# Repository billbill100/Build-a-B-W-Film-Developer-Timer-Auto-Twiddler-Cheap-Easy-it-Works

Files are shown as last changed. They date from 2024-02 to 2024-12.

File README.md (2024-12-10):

# Build-a-B-W-Film-Developer-Timer-Auto-Twiddler-Cheap-Easy-it-Works

Following on from my successful 'Build a shutter tester for focal plane shutters, cheap, easy & it works'

Here is my design of a timer for B&W film developing.

Many, like myself, use a stopwatch or a three line LCD timer, however, I thought it would be good to move into the 21st century with a colour screen & better functionality.

The developing timer allows the user to easily program the, initial & secondary agitations and interval, as well as stop & fix times, by turning a dial.

The screen then steps though each process, showing green when running, yellow to give a 10 second warning of an action to take place (agitation for example)
and then highlighted as the user has to carry out the action. Finished tasks then become grey. An audible cue will also be added.

Additionally, for twiddlers like myself, the timer drives a stepper motor to carry out all of the development agitation tasks & also stop & fix agitation if required. I will leave the debate as to whether to twiddle or not, to others.
Myself, I find it much easier to leave the developing tank in the water bath and twiddle. It maintains a better temperature, does not aerate the developer, stops water dripping & alleviates the threat of spillage during agitations.

The hardware is all cheaply available on Aliexpress & uses many of the same parts as the shutter tester. Where possible, I have kept the wiring identical.
Basic practical skills are required to build the timer. All of the required electronic modules are pre-built, so there is little or no soldering required, as push-fit or screw terminals are used for the connections.

Optionally, a li-po battery can be added, which is automatically charged & will power the timer in the event of a power failure.

Forum can be found here
https://www.photrio.com/forum/threads/build-a-b-w-film-developing-timer-twiddler-cheap-easy-it-works.204682/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

On first startup, the screen will show an Authorisation Code and ask that a User Key be entered. To obtain the User Key, contact me via message and the key will be issued free of charge. Please note this key is will last the lifetime of your project. It only needs entering once but make a note of it (write on a piece of paper & leave in the project box) in case a Factory Reset is performed.

The User key is issued free of charge, and there will never be any charge made for this key. It has been added to stop piracy and users being charged for firmware downloads.

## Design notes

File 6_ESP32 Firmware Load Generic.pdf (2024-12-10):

### ESP32 Firmware Load. Generic V1.0 27/10/2024

Download the code from the required github page.

click on the green <>Code button, which will allow you to download all of the files as a zip file. Unzip (extract) the downloaded file.
https://github.com/billbill100
Download the Flashing software.

A program called Flash Download Tool is required. It is included on the Github page, or can be downloaded from
Tools | Espressif Systems (https://www.espressif.com/en/support/download/other-tools)

Unzip (extract) the folder and put the files somewhere suitable on the computer. The software is stand-alone and does not need to be installed.
Checking the ESP32 USB driver.

The USB driver should have been installed, following the driver installation guide. To confirm, after connecting the ESP32 board, press Windows key + x and select Device Manager. Look for the COM ports and expand. The ESP module should be seen, as in this example on COM port 6, showing the CP2102 driver.

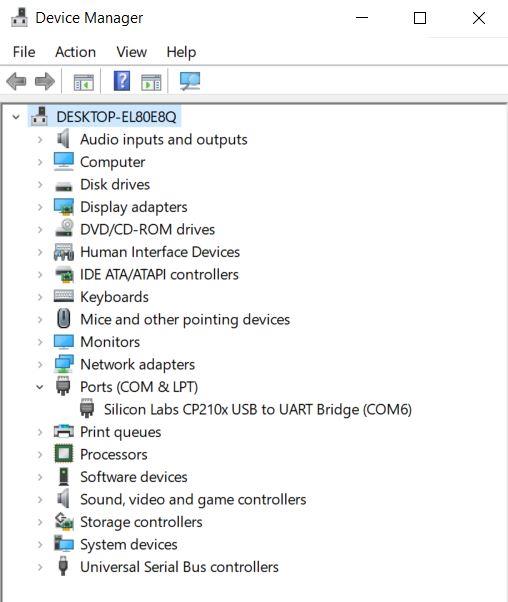
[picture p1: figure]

If the driver is missing, as shown on the screen below (Yellow Triangle) refer to the document Installing CP2102 Driver. Found in the Github repository.

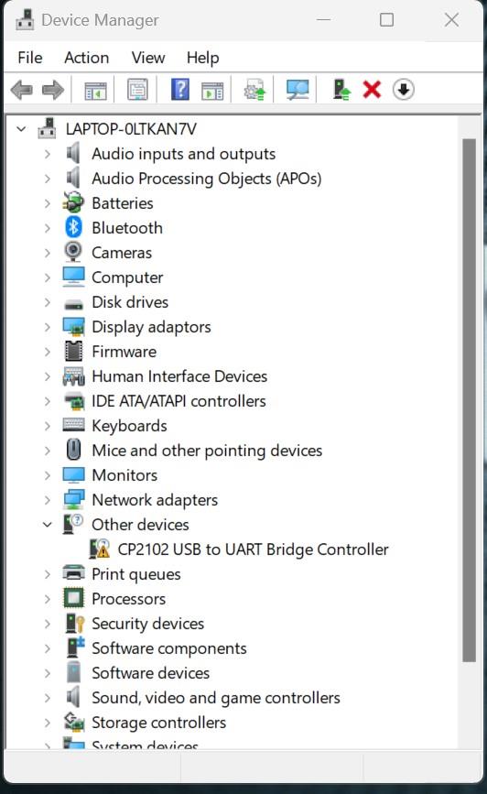
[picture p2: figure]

### Flash the Shutter Tester firmware to ESP32

Find the folder where the Flash Download Tool files were extracted to.

Launch the Flash Download Tool by double clicking on ‘flash_download_tool_3.9.5.exe’

Select ‘ESP32 from the drop-down box, as shown in the screenshot below and click ok.

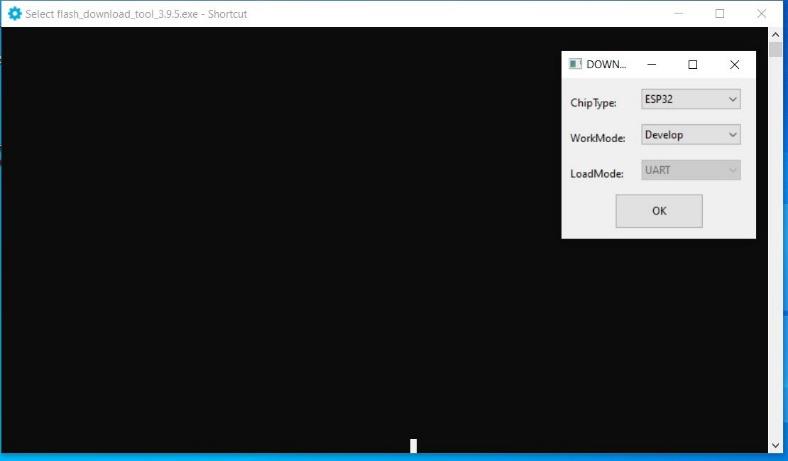
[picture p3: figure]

A screen like the below will appear and must now be populated. (The two windows can be moved as required)

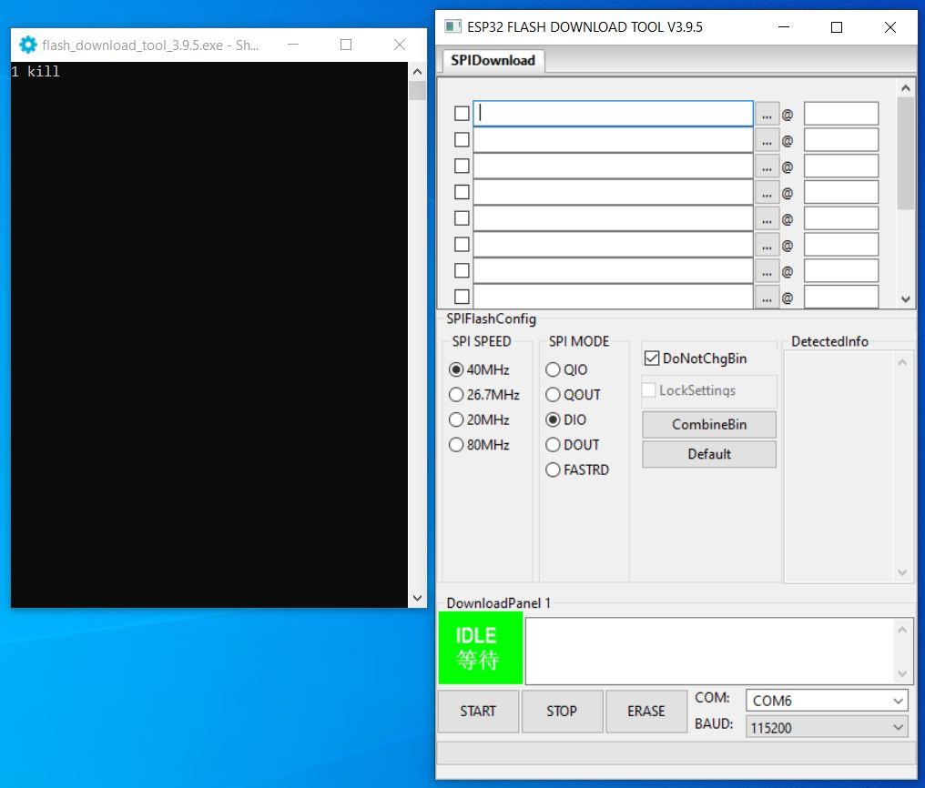
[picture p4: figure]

### Populate the values as follows

1) Click the three dots, navigate to, and select the downloaded file bootloader.bin Do the same on the second line, selecting partitions.bin
and again for the third line firmware.bin
If the files are selected correctly, the black window (5) will show each file name
2) Type 0x1000 into the top box, 0x8000 into the second and 0x10000 into the third.
3) Tick the three boxes next to the file names
4) Select the correct COM port from the drop-down box

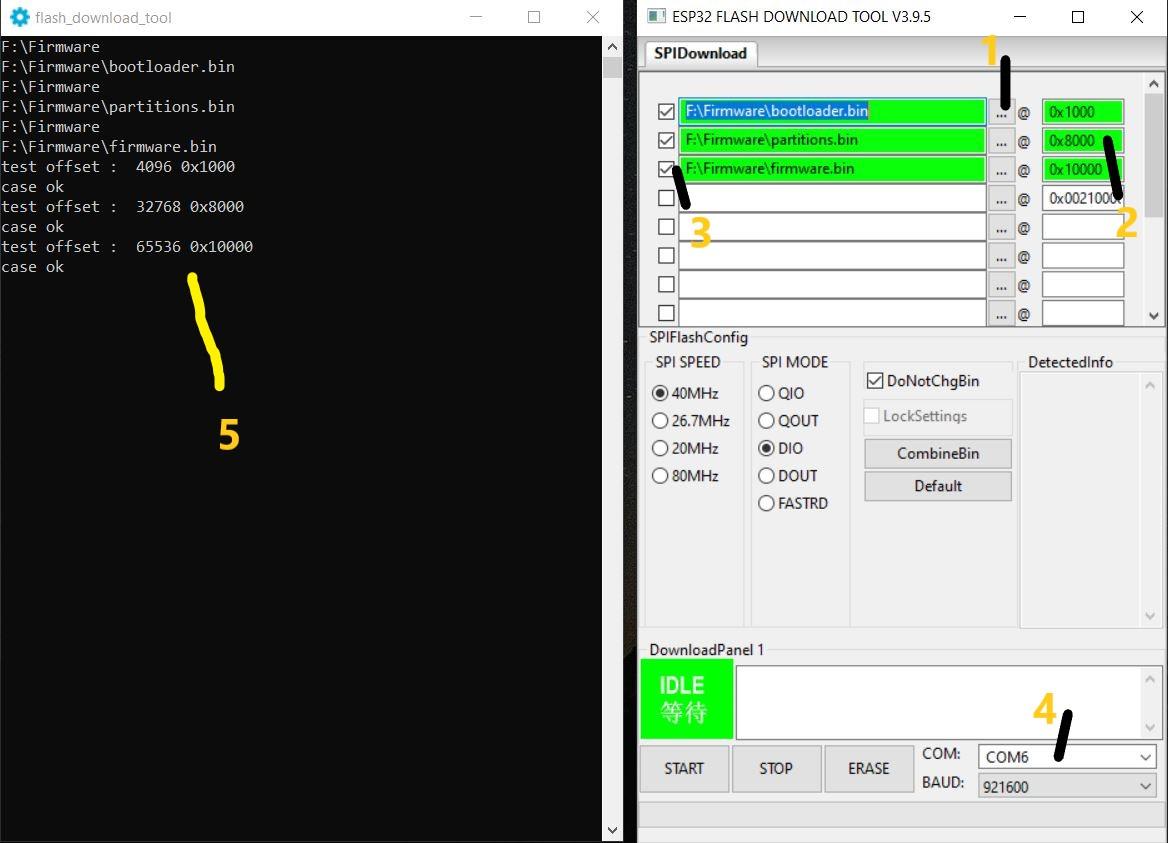
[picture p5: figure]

The file names and number boxes will be green, if the Flash Download Tool as found the files & is happy with the values.

Note: - If any of the file names or numbers did not turn green as they were selected & the black window report ‘case ok’, then there is an issue with the downloaded flash files, or the stored location on the computer.

Now press ‘START’ At the bottom left of the box. The green ‘IDLE’ box will change to ‘SYNC’

A line of dots will appear on the black screen, press either the BOOT button on the ESP32 board or Red Button for 3 seconds and then release.

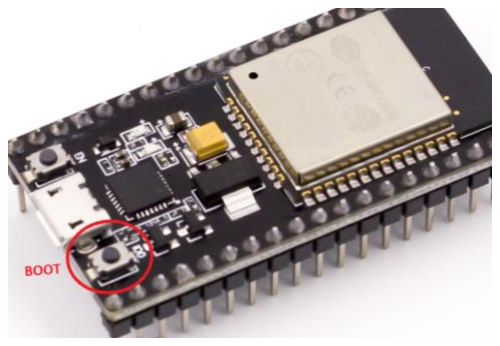
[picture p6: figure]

If successful, a screen, as below, will be seen. The Black screen will show the flashing to the device. A green progress bar blue box will appear in the other screen, then the green start button will change to a blue ‘FINISH’

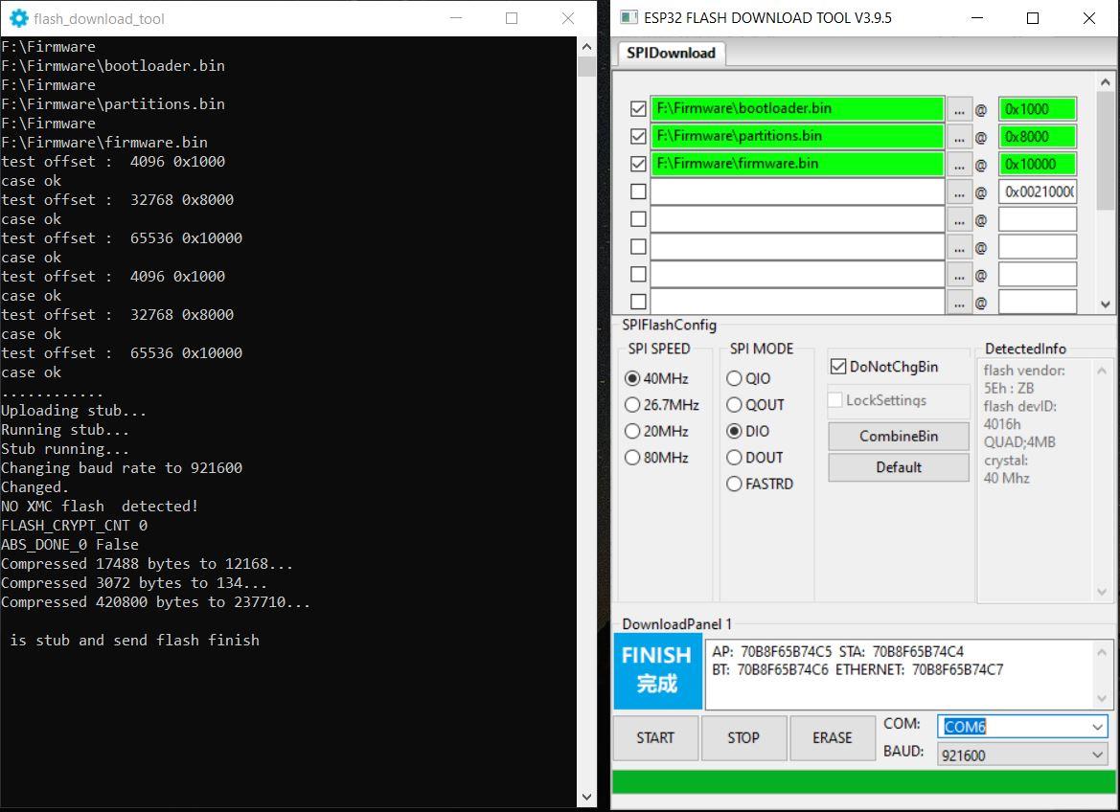
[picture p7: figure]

Note: - the flashed code will not start running until either the Reset button has been pushed on the ESP32 board (located on the other side of the USB connector to the Boot button) or a perform a power reset.

If problems occur, check the following: -

Remove & insert the USB cable into the computer. Windows, by default will make a sound indicating a USB device has been connected.

Open Device Manager and check the ESP32 board is shown. Removing & re-inserting the USB cable will make the ESP32 disappear & re-appear.

Ensure there is no yellow warning triangle by the COM port in Device Manager, indicating the device driver is not loaded.

Try changing the baud value to 115200 and try again.

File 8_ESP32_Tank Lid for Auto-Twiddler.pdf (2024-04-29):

I would really be grateful if you start to build the Developing Timer, that you go to the Photrio thread and say hi. Also please post photos of your completed tester.

Please refer to Photrio for further build help & to let us know you are building the timer.
Build a B&W film developing timer & twiddler - Cheap, Easy & it Works | Photrio.com
Photography Forums (https://www.photrio.com/forum/threads/build-a-b-w-film-developing-timer-twiddler-cheap-easy-it-works.204682/)

GitHub repository where all documentation & code can be found. billbill100 (github.com) (https://github.com/billbill100)

## ESP32 Developer Timer Tank Lid V0.9 28/05/2024

The debate as to whether to twiddle or invert will go on forever.

Personally, I'm a twiddler. Using a water bath & twiddling, means the tank stays in the water bath for the full development time, thus maintaining a stable temperature.

Inversion can also cause over agitation and additional unwanted aeration of the chemicals. Especially if using a double reel tank with just a single film. Ilford themselves warn of this.

There is the issue of water splashes all over the place when agitating. There is also the increased risk of chemical spills, should the lid leak or has not been seated correctly.

As I use the water bath for the final rinse, I do not want the water contaminated with chemicals.

The development Timer incorporates the option to fit a stepper motor, which will carry out all of the twiddles.

For users of the Patterson Super 4 tank, two files are attached, to 3d print a tank lid incorporating the stepper motor fixing holes and teeth to engage with the tank serrated edge.

An adaptor to connect the stepper motor output to the twiddling stick is also included. (coming soon)

Without a 3d printer, a suitable lid can easily be cut from a piece of ply or plastic. It is important that the lid cannot rotate, else there is the possibility of it turning, rather than the reels. With the Patterson Super 4, this is easy to achieve due to the serrated rim of the tank.

There are two stl files available, to 3d print

Patterson Tank Lid.stl incorporating a stepper motor mount & teeth to engage with the Patterson tank rim.

Twiddle Stick.stl A replacement twiddling stick that mounts directly to the stepper motor shaft.

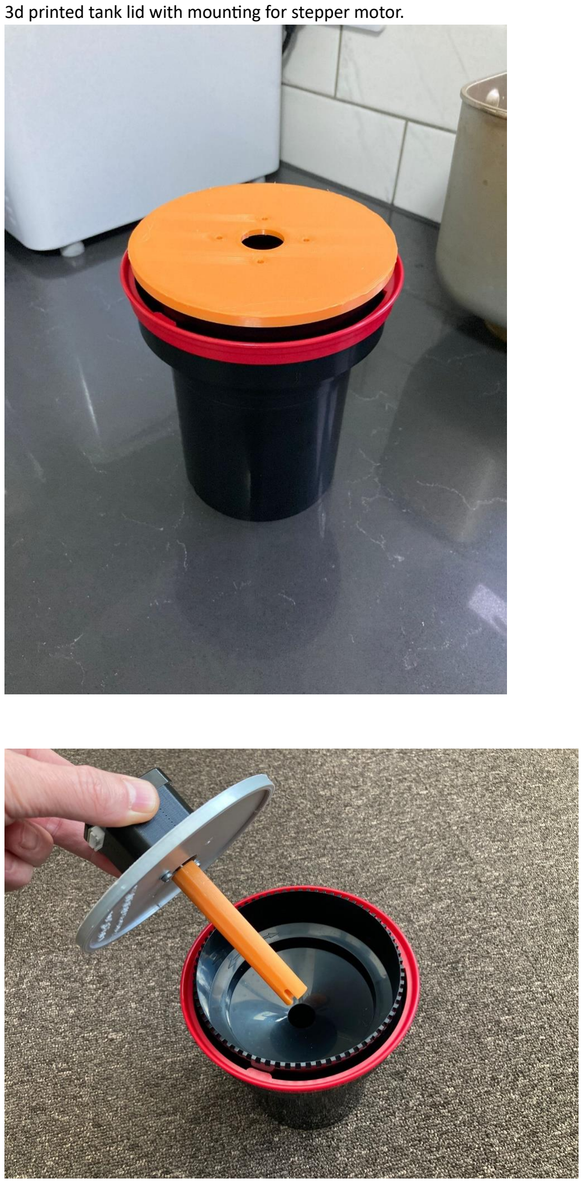
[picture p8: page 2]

3d printed tank lid with mounting for stepper motor.

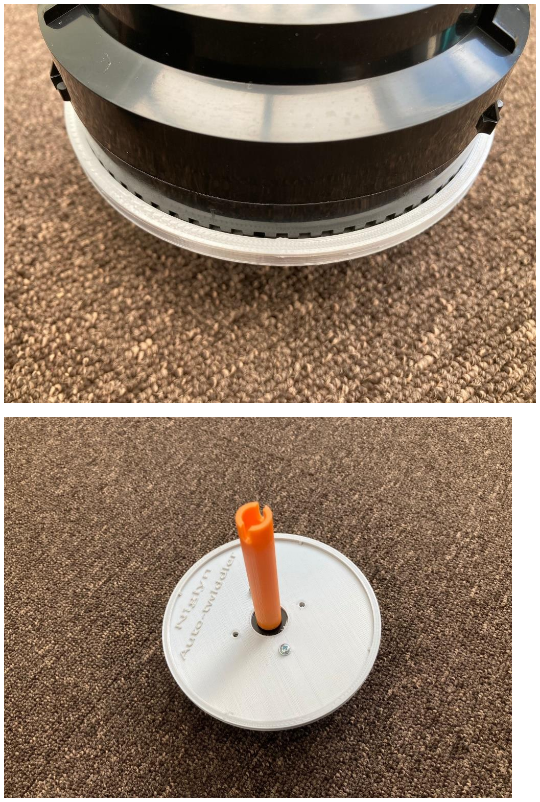
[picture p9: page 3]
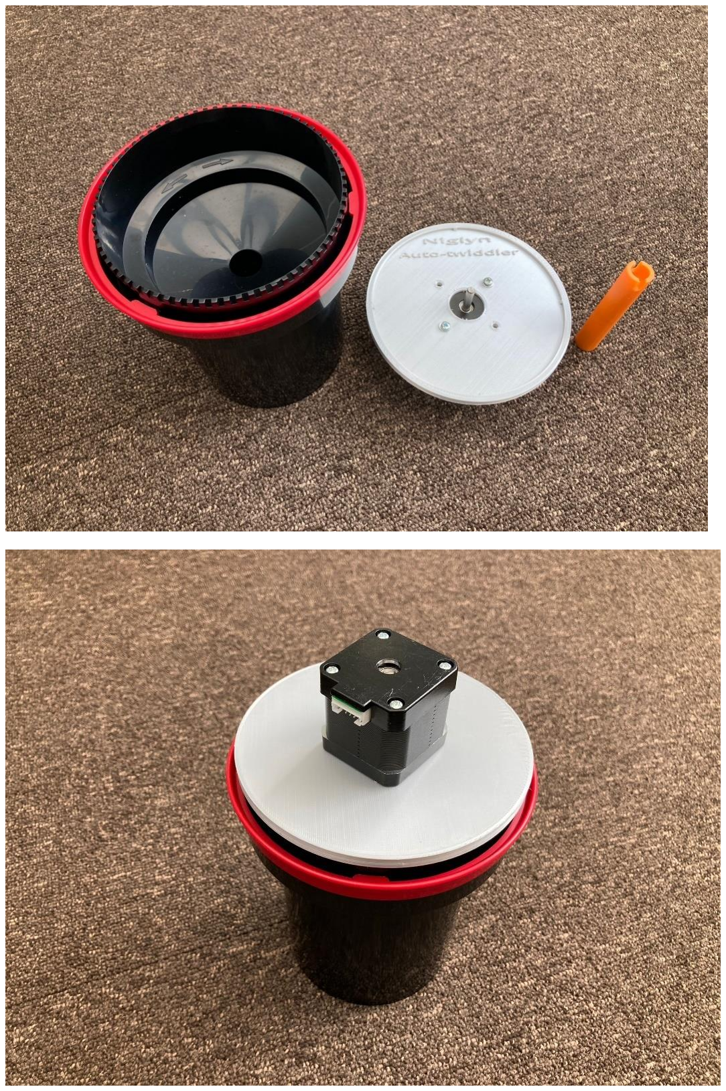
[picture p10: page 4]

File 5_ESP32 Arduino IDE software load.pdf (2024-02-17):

### ESP32 Arduino IDE Software Load. V1.2 21/01/2024

Note:- The guides below must be followed in the correct order ESP32 Installing CP2102 USB Driver
ESP32 Arduino Software Load
ESP32 Firmware Load

Both Nano & ESP32 use the same computer program, Arduino IDE to display the Shutter Tester output to the computer screen.

Arduino IDE (Integrated Development Module) is a computer program used to communicate with the Arduino processor boards, Nano, for example. The program allows writing & development of Arduino code and has many other features and uses.

One such feature, is the ability of the Arduino module or ESP32 to send data directly to the program for display on the computer screen. This is called ‘Serial Monitor’.

This feature is used to display not only the same information as that of the LCD, but also far more, that simply would not be possible with the LCD alone.

Download the software
To get started, download the Arduino 2.x software from
Software | Arduino (https://www.arduino.cc/en/software)

Install the software
To watch a tutorial for the install process, watch this video up to 6.04
(284) How To Install Arduino IDE 2.0 On Windows 10/11 [ 2023 Update ] Arduino Uno Complete Guide - YouTube (https://www.youtube.com/watch?v=2AZQfieHv9g&ab_channel=GeekyScript)

Note:- The video past 6.04 is not applicable for our use and will not work with ESP32 unless additional definitions are loaded. Details of how to load the definitions, for those wanting to learn programming of the ESP32, can be found at the end of this document.

That is it. The software can be run.

1 Connect the ESP32 board to the computer with a suitable USB cable.

2 Select Arduino Nano and the correct COM port

3 Change the baud to 115200 (This is just a test, change the baud to 460800 when using with the shutter tester)

4 Open Serial Monitor window. This opens at the bottom, but can be dragged up to make it larger.

5 Press the Reset button on the ESP32 module and the bootloader output will be seen in the Serial Monitor window.

Success :o)

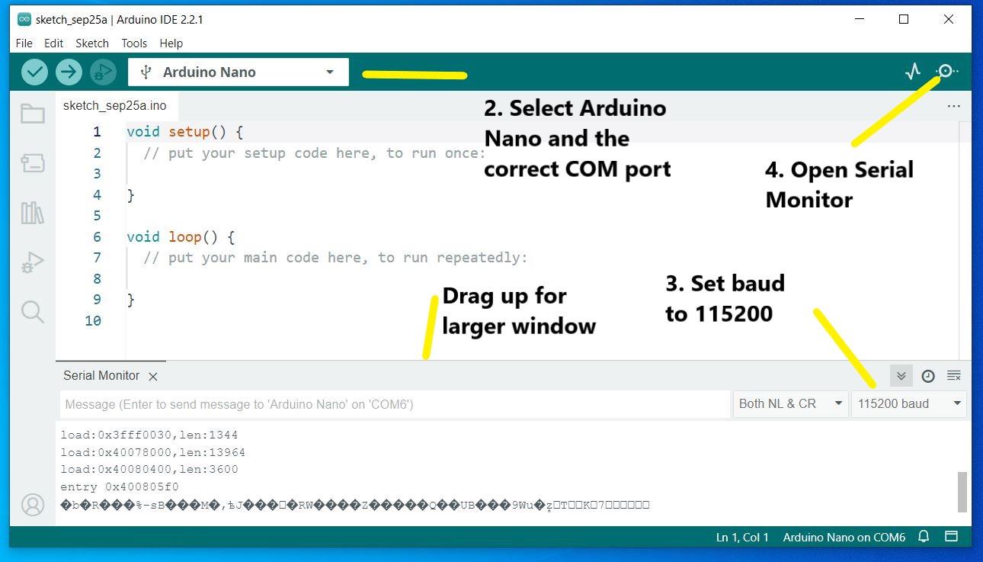
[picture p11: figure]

Optional Steps.
This software is only used to display the output from the Shutter Tester via the USB connection and using the ‘Serial Monitor’ screen in ‘Arduino IDE’.

To write and load code to ESP32 processors, additional processor definitions have to be loaded. These are NOT necessary for use with the shutter tester, but for those that wish to experiment with the ESP32 and write their own code, details of the additional steps required are detailed below.

Add the ESP32 definitions
To add the extra ESP32 definitions, follow this video
(296) ESP32 install Arduino IDE 2 in 90 seconds #ESP32 - YouTube (https://www.youtube.com/watch?v=mwi01JG_OGA&ab_channel=ProgrammingElectronicsAcademy)

At 1.15 in the video, select NodeMCU-32S. Also ensure the correct COM port is selected.

Load a sketch onto the ESP32
Now go back to the ‘How To Install Arduino IDE’ software install video and load the Blink sketch as described from 6.04, ensuring NodeMCU-32S is selected for the board.

Note:- when ‘Connecting’ is shown on the lower screen, the Boot button on the ESP32 board must be pressed and held until the code starts to load (around three seconds)

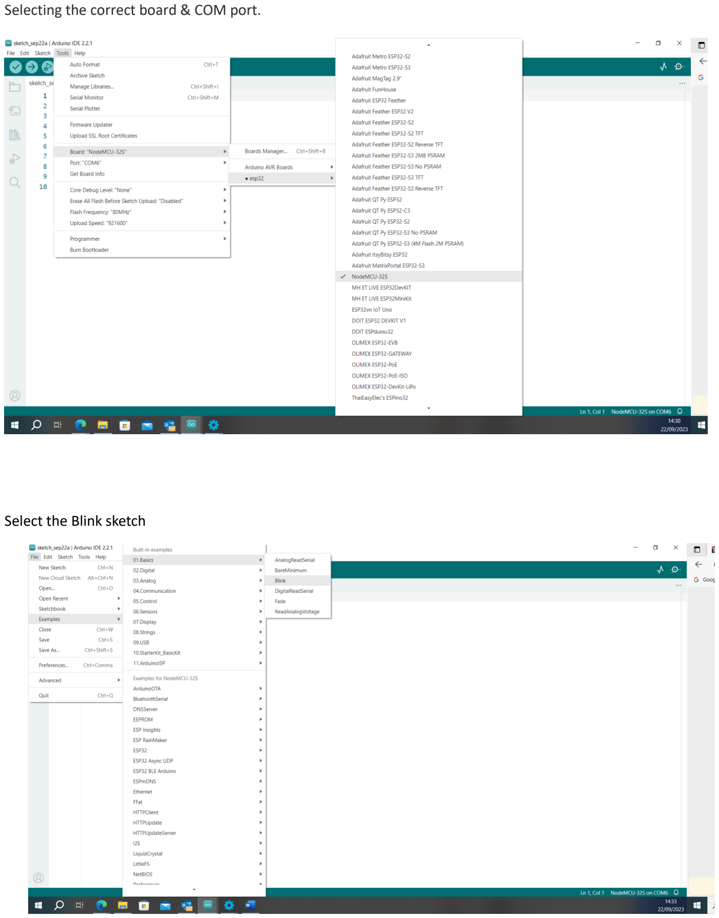
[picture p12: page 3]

Selecting the correct board & COM port.

Select the Blink sketch

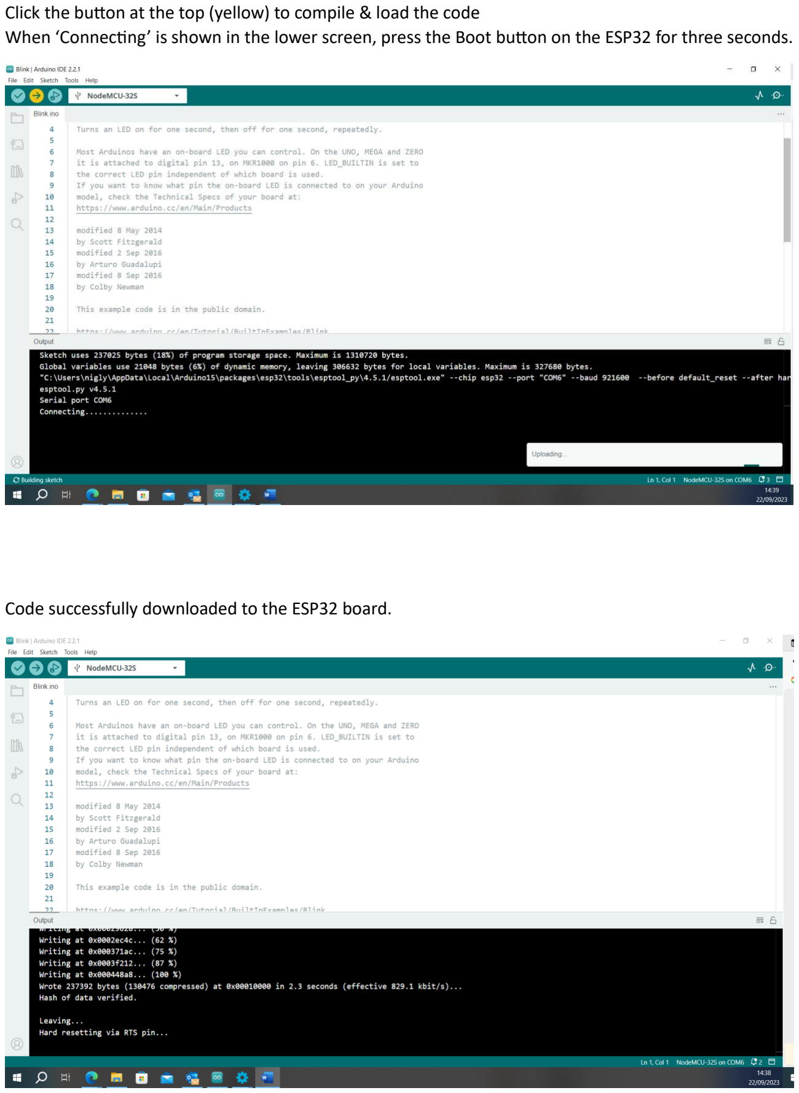
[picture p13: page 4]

Click the button at the top (yellow) to compile & load the code
When ‘Connecting’ is shown in the lower screen, press the Boot button on the ESP32 for three seconds.

Code successfully downloaded to the ESP32 board.

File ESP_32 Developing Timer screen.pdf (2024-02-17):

I would really be grateful if you start to build the Developing Timer, that you go to the Photrio thread and say hi. Also please post photos of your completed timer.

Please refer to Photrio for further build help & to let us know you are building the timer.
Build a B&W film developing timer & twiddler - Cheap, Easy & it Works | Photrio.com
Photography Forums (https://www.photrio.com/forum/threads/build-a-b-w-film-developing-timer-twiddler-cheap-easy-it-works.204682/)

V1.0 10—2-2024

The screen is a 4” TFT display, measuring 60 x 90mm, so plenty big enough to see. Below are some early screenshots. The current verson has improved display.

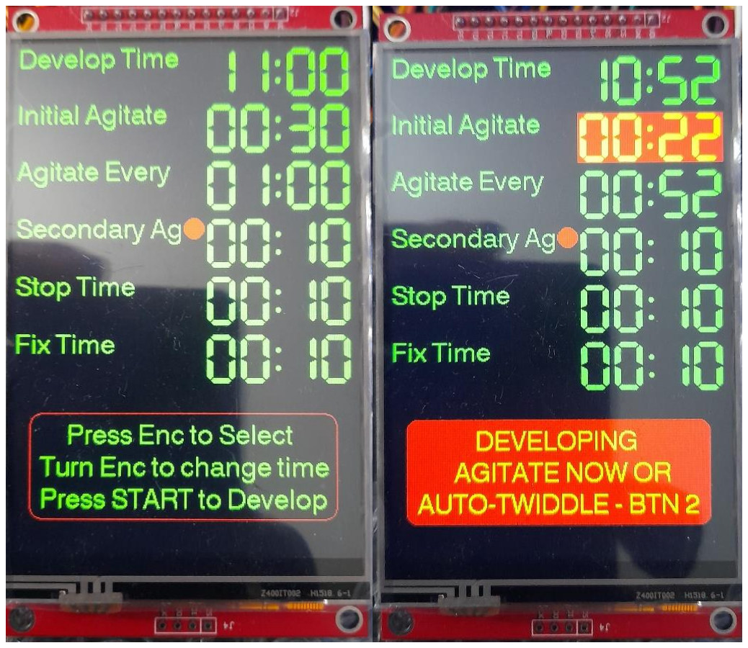
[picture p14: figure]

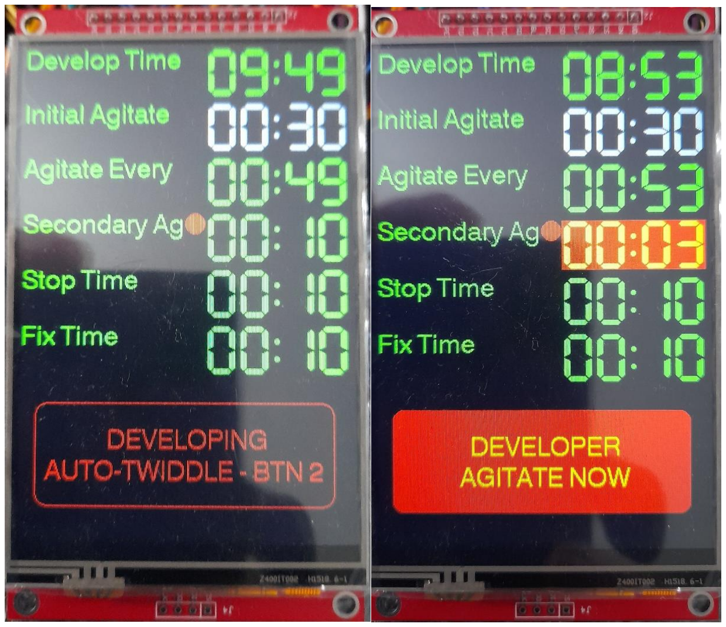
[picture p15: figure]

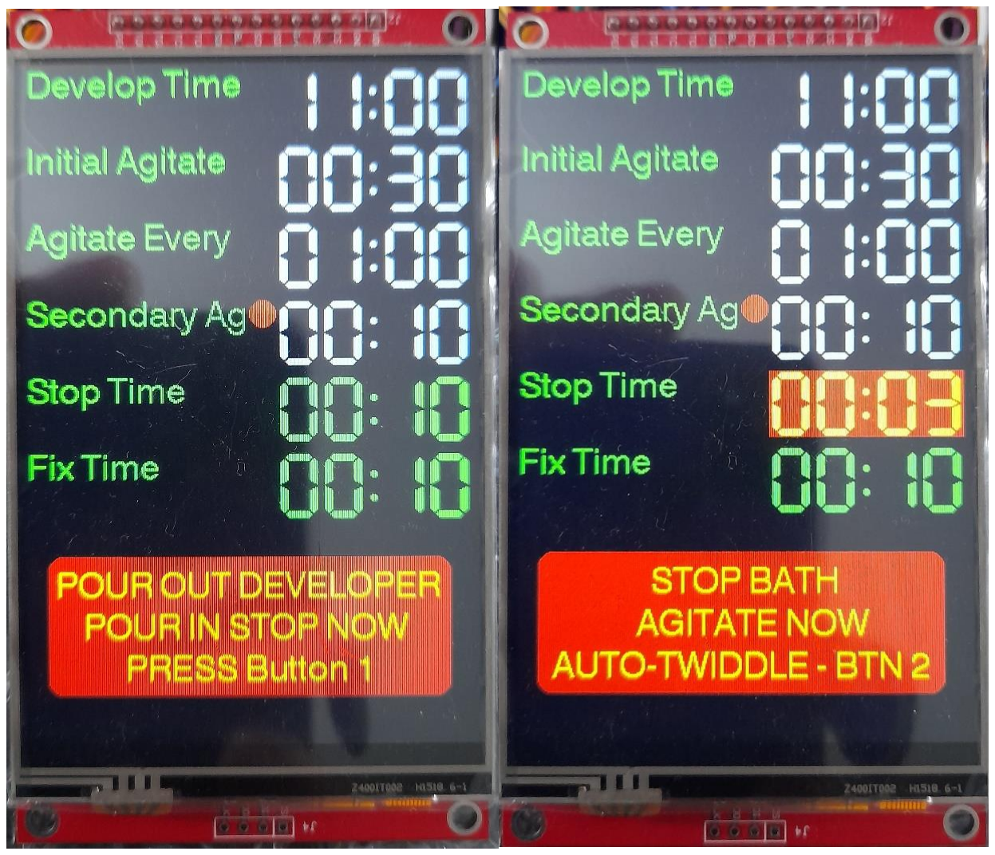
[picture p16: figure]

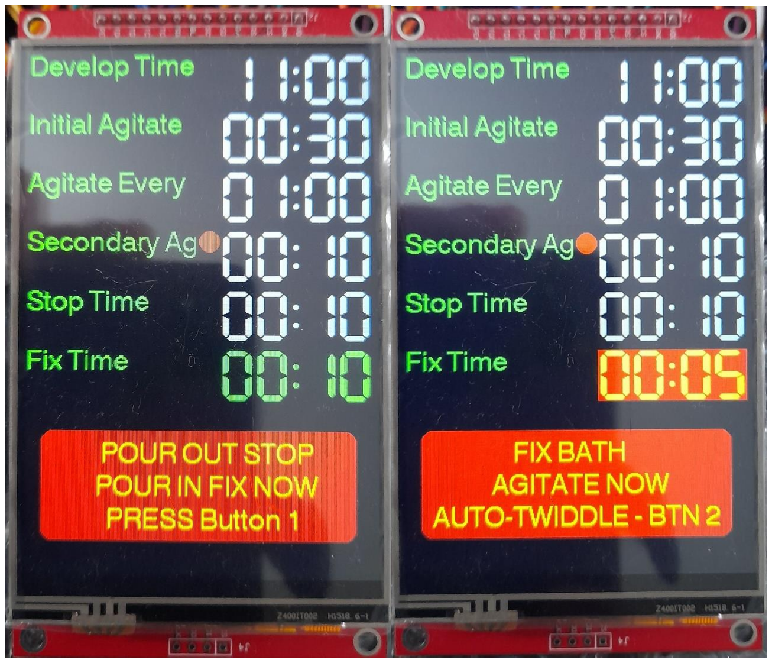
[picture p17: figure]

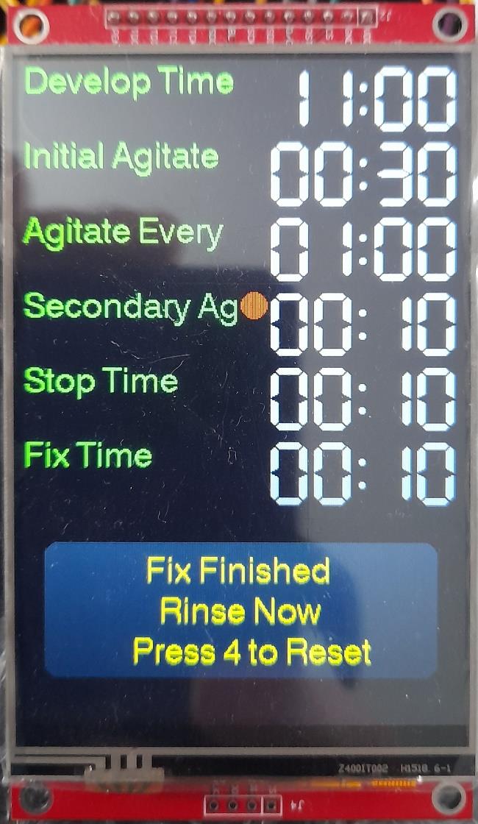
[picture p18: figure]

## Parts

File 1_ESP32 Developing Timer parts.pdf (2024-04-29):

I would really be grateful if you start to build the Developing Timer, that you go to the Photrio thread and say hi. Also please post photos of your completed tester.

Please refer to Photrio for further build help & to let us know you are building the timer.
Build a B&W film developing timer & twiddler - Cheap, Easy & it Works | Photrio.com Photography
Forums (https://www.photrio.com/forum/threads/build-a-b-w-film-developing-timer-twiddler-cheap-easy-it-works.204682/)

GitHub repository where all documentation & code can be found. billbill100 (github.com) (https://github.com/billbill100)

### ESP32 Developing Timer Parts V1.4 28/04 2024

Below are links to the parts required to make the ESP32 Developing Timer.

Links are valid now, but of course could become dead in the future.

Links are a guide only. Use a supplier that ships your country.

Ordering from China either from eBay sellers or AliExpress, the parts will be much cheaper.

Note, often if buying from AliExpress, there is a free express shipping option, if buying parts over a set value.

### 1. ESP32 Development Board. NodeMcu OR Lolin D32

Pick ONE of the two development boards below. Either will work. The NodeMcu comes with header pins pre-soldered, but there is no socket for battery backup or charging,

The Lolin D32 requires the header pins soldering, but has the advantage of connection of a backup battery & charging.

### ESP32 NodeMcu board. 38 pin version. USB-C CP2102

ESP-WROOM-32 ESP32-S Nodemcu ESP32 Development Board ESP32 Bluetooth Wifi 32Mbit SPI Flash Bluetooth Module ESP32 30 Pin/38Pin - AliExpress (https://www.aliexpress.com/item/1005005917503049.html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)

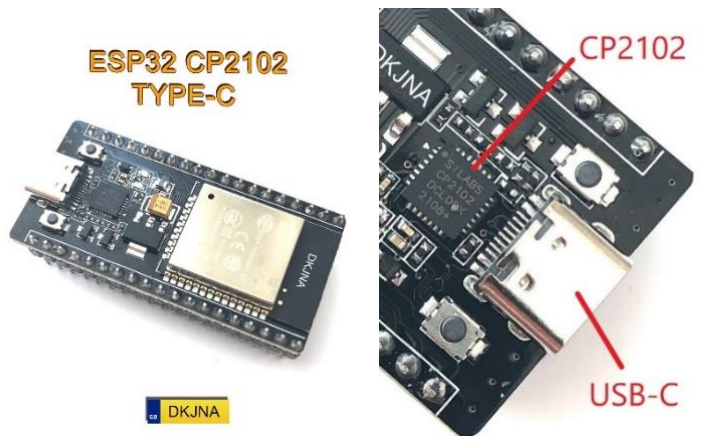
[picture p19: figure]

IMPORTANT. There are multiple variants of this board. Get 38 pin USB-C and CP2102 chip.
Note:- The guides have been written for this specific board type. Boards which differ with their USB chip and/or connector will still work, but the guides will not detail different driver installs or pin layout differences.

### ESP32 Lolin Wemos board

LOLIN D32 V1.0.0 - wifi+bluetooth board based ESP-32 esp32 ESP-WROOM-32 4MB FLASH Arduino MicroPython Compatible - AliExpress 502 (https://vi.aliexpress.com/item/1005006246561853.html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)

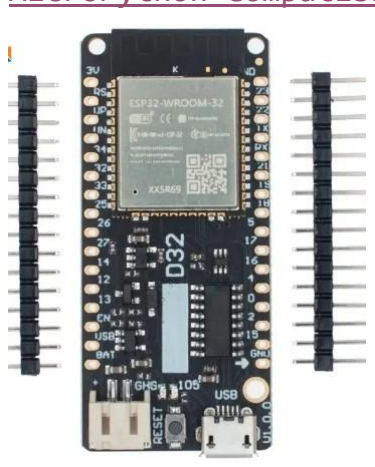
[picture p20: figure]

2. ESP32 prototype/breakout board (38 pin screw-terminal version).

Note:- You need this board regardless of the ESP32 board choice. If using the Lolin board, the breakout board legends will not match, so pay attention to the wiring guide.

ESP32 Expansion Board Compatible with ESP32 WiFi Bluetooth Development Board NodeMCU-32S Lua 38Pin GPIO Expansion Board - AliExpress (https://www.aliexpress.com/item/1005005677080016.html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)

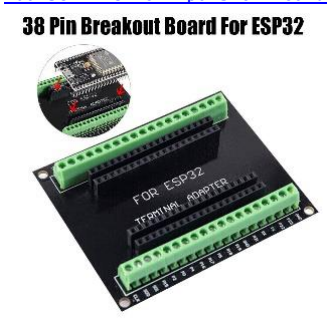
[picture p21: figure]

3. Button Module.

There are all sorts of buttons available, feel free to choose different ones depending on your final design. This module has the advantage of header pins for use with Dupont jumper wires & is great for development, but the coloured buttons below will be better for the final build.

DIY Kit 1x4 4 Independent Key Button Keypad Keyboard Module Mcu for Arduino Student Class Design Graduation Project Experiment - AliExpress (https://www.aliexpress.com/item/1005002483504604.html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)

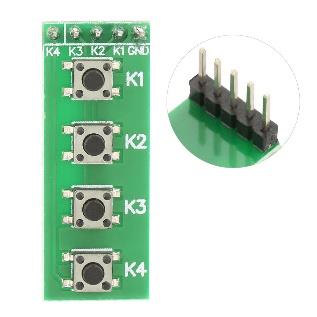
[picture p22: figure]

4. Buttons.

If mounting in a project box, these buttons are easier to fit and make a nice-looking project. The display will state which colour button to push, Green for the Start Button, Black for the reset & Yellow for the optional motor twiddler. Note:- This set is pre-wired, so no soldering is required.

DaierTek 5PCS 12mm Momentary Push Button Switch On Off Mini Round Switch Waterproof PBS-33B 3A 125V AC with Pre-soldered Wire - AliExpress (https://www.aliexpress.com/item/1005005789195514.html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)

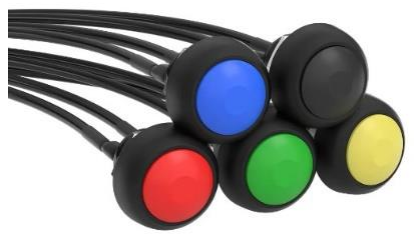
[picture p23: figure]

Below is a link to buttons which maybe purchases as a 6-pack, including a white button, or individually. They have the advantage of including a white button, which whilst not used at present, would be the next colour to be used if an additional button is required in future development. (Red is used for E-stop & the encoder knob is Blue, so whilst the builder could use either of these colours from the pack, they would not match the on-screen prompt). Note these buttons require soldering & are slightly shorter than the pre-wired buttons.
6piece Mini 12mm Waterproof Momentary On/off Push Button Round Switch Pbs-33b Kit White Black Red Yellow Blue Green - AliExpress (https://www.aliexpress.com/item/1005006228814305.html)
5. Dupont wires.
Get male to female Dupont Wires if using the screw terminal prototype board.
Two packs of 10cm for connection to buttons, tft, encoder etc.
Two pack each, 20cm wires

Dupont Line 10cm 20cm Dupont Cables Male To Male Female To Female Male To FeMale Jumper Wire, for Arduino DIY Electronics KIT - AliExpress (https://www.aliexpress.com/item/1005006263457745.html?scm_id=1007.40050.354490.0&scm-url=1007.40050.354490.0)

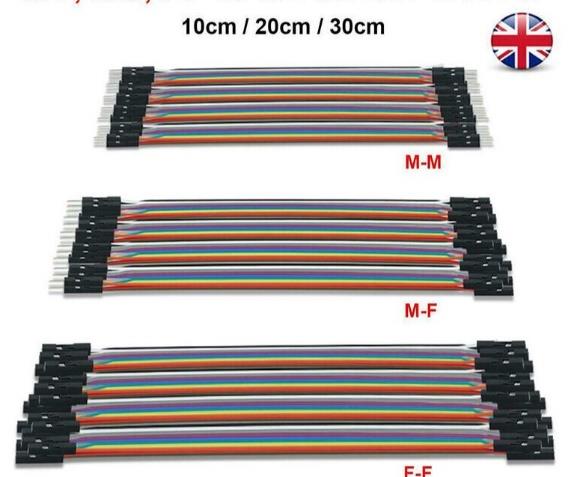
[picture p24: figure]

6. Brown & Black Dupont wires – Not Requied.
Note. There are enough of each colour if buying two packs each of the multi-coloured dupont wires detailed below, so additional single colours are not needed for the Development Timer, however a link to single colours is left here as having additional Brown (3V) Red (5V) & Black (0V) can be useful for other projects.

10pcs Breadboard Dupont Cable For Arduino Line 2.54mm Male Female Dupont Jumper Wire 26AWG Cable DIY Electronic 1P Connector - AliExpress (https://www.aliexpress.com/item/1005004062117789.html)

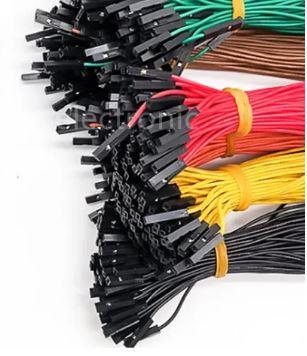
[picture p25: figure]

### 7. Connector block (optional)

There are many 3V & 0V wires to be connected. The best way to accomplish this is to use a choc-bloc to group all of the wires together & then just one wire from here which then connects to the breakout board. Alternates are to solder them together, or use a joining block similar to the below.

10-75pcs Orange Universal Type Quick Plug-in Terminals,Electrical Equipment Connectors,Wire Connector Terminals,250V/32A - AliExpress (https://www.aliexpress.com/item/1005006271613810.html?scm_id=1007.40050.354490.0&scm-url=1007.40050.354490.0)

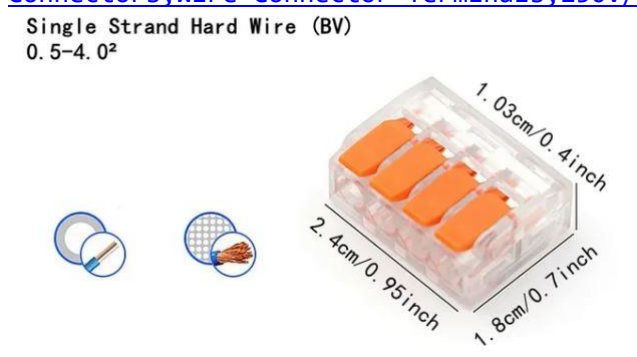
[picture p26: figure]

8. TFT display.

### 4.0 inch SPI module 3.95 inch ILI9488 14 pin TFT LCD display scree Resistance touch panel

PCB adapter base board 2.54 mm spacing (sic)

Board size is 108.04 X 61.74

(The above, including mis-spelling, is taken from AliExpress listing, to help ensure the correct tft screen is purchased

Note:- There are many similar modules but they have different driver chips (ILI9488), the Develop Timer only works with this specific module. Please ensure you correctly order the module. The Aliexpress web sites often list similar but different modules & sometimes just the bare screen. The 4.0” specified for this project module does not have the 5V regulator populated on the board. (circled).

4.0 inch SPI module 3.95 inch ILI9488 14 pin TFT LCD display scree Resistance touch panel PCB adapter base board 2.54 mm spacing - AliExpress (https://www.aliexpress.com/item/1005003033828159.html)


Note:- regulator (U1, written upside down) is not populated on this board.

9. Rotary Encoder.
Ensure you purchase the one with blue pcb as shown below.
With Switch Rotary Encoder Module for Arduino Brick Sensor Development Round Audio Rotating Potentiometer Knob Cap EC11 - AliExpress (https://www.aliexpress.com/item/1005001696915804.html)


### 10. Piezo Sounder. (optional)

Audibly warns when next user operation is required (agitation, pour out dev, end of process)

10PCS Passive Buzzer AC 12MMx8.5MM 12085 42R Resistance 3V 5V 9V 12V In Common Use Mini Piezo Buzzers For Arduino Diy Electronic - AliExpress (https://www.aliexpress.com/item/4000148640191.html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)


### 11. Project Box. (optional)

There are all sorts of shapes & sizes of project boxes. The 158 x 90 x 60 is a good size if not using the auto-twiddler. The screen must be positioned as high as possible, to leave enough space below, for two rows of buttons. Refer to cutting template.

If fitting the optional stepper board for auto-twiddling, whilst the stepper board can be squeezed it, it is a very tight fit, so using a larger project box maybe easier.

Black Box Outdoor Waterproof Case Plastic Box Electronic Project Case Instrument Waterproof Junction Box Housing - AliExpress (https://www.aliexpress.com/item/1005005622148025.html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)


### 12. Hook-up wire. (optional)

To make all the soldered connections to buttons, sockets etc, jumper wire is required. You could just by a reel of one colour, or use wire from an ethernet cable. Or buy a box of multi-colour cable.

Here is a link to wire in a dispenser box. Buying both box 1 and box 2 will match the Dupont wire colours. Get 22AWG High quality super soft silicone wire and cable household DIY 5 colors mixed box wire tinned pure copper (aliexpress.com) (https://vi.aliexpress.com/item/1005001623151797.html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)


13. Li-Po Battery (Optional, only for use with Lolin D32 board) With JST PH2.0 connector.
The prototype was built using the 1000mAh battery. A 2000mAh battery should also work well. If using a different battery to the ones specified below, ensure they have the little pcb at the top, which gives unde-voltage & over-current protection.

523450/503450 1000mAh 3.7V Polymer Lithium Rechargeable Battery Li-ion Battery JST PH2.0 2pin For GPS Smart Phone DVD MP5 - AliExpress (https://www.aliexpress.com/item/1005003198563309.html)

100% real capacity 3.7V 103450 2000mAh Rechargeable Polymer Lithium Battery, for Cameras, GPS, Bluetooth Speakers，PS4 controller - AliExpress (https://www.aliexpress.com/item/1005004204694483.html)


Red & Black Pins require removal from plastic housing and swapping round.

Caution – There is no standard for the polarity of the battery connector. Check and double check the red & black wires are the correct way round on the battery connector, to match the Lolin processor board. If they are not, carefully lift the plastic locking tab on the connector, securing the pin & slide out. Do this for both pins, taking care not to let them touch. Then re-insert the correct way round. The batteries specified above have the connector pins the wrong way round and will need to be swapped.

### 14. On/Off switch. (Optional)

Use if fitting the Li-PO battery, else when disconnecting the Developing Tomer from the USB or 12V power, the Developing Timer will continue to run on battery.
10Pcs SS22F32 6 Pins 2 Positions DPDT On/On Mini Slide Switch 0.5A Toggle Switch Y5GB -AliExpress (https://vi.aliexpress.com/item/1005003660190950.html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)

Optional Parts if Automatic Twiddling is required.

Cavet Whilst the stepper motor works fine in testing, it has never been connected to a twiddling stick. The user will have to build their own mounting frame to hold the stepper and devise a method of connecting to a twiddling stick to the motor shaft. Using flexible plastic tube should work.

a. Stepper Motor.
Ensure the version with XH line is selected. This will then fit the driver breakout board.

3D Printer Parts Nema17 17HS4023 for Titan Extruder 4-lead Nema 17 22mm 42 Motor 0.7A 12V 14N.for 3D Printer Motor - AliExpress (https://www.aliexpress.com/item/1005004963609855.html)


b. Stepper Motor Driver Board.
The version 2 board has the adjusting potentiometer mounted on the top (can be seen just in front of the blue heatsink) making it much easier to adjust than the earlier version.
TMC2208 TMC2209 ATD5833 V2.0 With Heat Sink Stepper Motor Driver StepStick 3d Printer Parts 2.5A 256 Subdivision Silent Printing (aliexpress.com) (https://www.aliexpress.com/item/1005004862737922.html?spm=a2g0o.cart.0.0.bf1a38daaEBcBB&mp=1)


c. Stepper Motor Breakout Board.
42 Stepper Motor Driver Expansion Board DRV8825 A4988 3D Printer Control Shield Module For Arduino 3 Ramps1.4 DIY Kit (aliexpress.com) (https://www.aliexpress.com/item/1005002915948304.html?scm_id=1007.40050.354490.0&scm-url=1007.40050.354490.0)


d. 12 Volt Power Supply.
A 12V 2A power supply is required to run the stepper motor. A socket could be mounted on the project box, for a neat connection, or use an adaptor (circled), or just cut the connector off & connect directly to the stepper board.
Note- Only the stepper uses 12V. The processor board still requires connection to a USB power supply. An alternate is to use a buck converter to convert 12V to 5V, negating the need for a separate USB power supply.

AC DC 12v 1A 2A 3A 2000ma 3000MA adapter power supply EU UK AU US PLUG 5.5*2.5mm wall charger for DC male female led strip light (aliexpress.com) (https://www.aliexpress.com/item/1005001731366424.html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)


### e. DC Power Jack. (Optional)

This will allow a socket to be fitted to the project box, for a neat looking solution.

5/10Pcs 5A 30V For DC Power Supply Jack Socket Female Panel Mount Connector 5.5mm 2.1mm Plug Adapter 2 Terminal Types 5.5x2.1 - AliExpress (https://www.aliexpress.com/item/1005004637388048.html)


### f. 12 Volt to 5 Volt buck converter. (Optional)

This will allow a single 12Volt connection to the project, to power both the steeper motor & processor board.

DC-DC 24V/12V To 5V 5A Step Down Power Supply Buck Converter Replace LM2596S Adjustable USB Step-down Charging Module For Phone - AliExpress (https://www.aliexpress.com/item/32785352477.html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)


Alternate power converter, smaller & cheaper, but requires soldering. (ensure the 5V version is selected) High Efficiency Output 3.3V 5V 9V 12V 5A mini560 Step Down DC-DC Converter Voltage Regulator Buck Stabilized Power Supply Module - AliExpress (https://www.aliexpress.com/item/1005005544927756.html)

### g. Diode. (Mandatory)

Fit If using a 12V to 5V regulator, a diode must be placed between the 5V output and the connection to the breakout board. This prevents 5V flowing back into the stepper board, which then tries to drive the stepper motor.

Order the 1N5404 diodes

High quality Rectifier Diode 1N4007 10A10 1N5408 1N5819 1N4001 5822 1N4001 1N4004 1N4005 1N5404 1N5408 6A10 FR107 UF4007 SR5100 - AliExpress (https://www.aliexpress.com/item/1005002872292563.html)

### h. Self Locking switch. (Optional)

Fit in-line with the stepper motor enable pin, to make an emergency stop button for the stepper motor. Select the Latching, Red option.

2PCS 12MM Mini 2pin Dome Push Button Switch OFF-ON Momentary Latching Waterproof Plastic Motorcycle (aliexpress.com) (https://www.aliexpress.com/item/1005003020720620.html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)


Additional useful parts

The design of the auto-twiddler is up to the imagination of the builder. A universal joint (5mm) is required to connect the motor to a shaft, which in turn will connect to a rod and then the twiddling stick.
The assembly must then be held in a frame above the developing tank, to engage with the spiral. The frame could be built the same width as the water bath, so it sit just outside, which will also ensure it is the spiral, not the frame, which turns.

Universal Joint
2/3/3.17/4/5/6/6.35/8/10mm Boat Car Shaft Coupler Motor Connector Metal Universal Joint Coupling - AliExpress (https://www.aliexpress.com/item/4000194793728.html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)

Drill bits for making encoder and button holes. 7mm for encoder, 13mm for the buttons.
3-12mm Three-point Woodworking Drill Hole Opener Twist Drill Bit Practical Wood Milling Cutter Multifunctional Drilling Tools - AliExpress (https://www.aliexpress.com/item/1005006103163521.html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)

13mm drill bit

10-35mm Woodworking Twist Drill Bit Set Long Four-Slot 6.35mm Shank Carbide Drill Bit Hole Saw For Door Lock Wood Slotting Tools (aliexpress.com) (https://vi.aliexpress.com/item/1005003944211081.html)

M3 Bolts, Nuts, Washers.
Depending on the final design, M3 bolts can be used to hold the tft screen, breakout-board and stepper driver.

https://www.aliexpress.com/item/1005005544927756.html?spm=a2g0o.order_list.order_list_main .96.18381802at3zUL

Glue Gun.
Cheap glue gun, but surprisingly it works ok.
20W Hot Melt Glue Gun DIY Mini Household Industrial Guns Heat Temperature Thermo EU Electric Repair Tool Use 7mm Glue Sticks - AliExpress (https://www.aliexpress.com/item/1005005795878015.html)

Soldering Iron Kit.

AliExpress have loads of cheap soldering irons. If buying one, wrap some kitchen foil between the ceramic heater, so the bit is a tighter fit. I found the one I bought lost heat too quickly, resulting in poor joints & melted plastic as heat had to be applied far longer. Mine went in the bin & I went back to an Antex soldering iron. You may have better luck.

### Change Log

V 1.1 changed piezo buzzer from active to passive buzzer Extra coloured buttons added

V1.2 Button link changed & diode added, bolts added

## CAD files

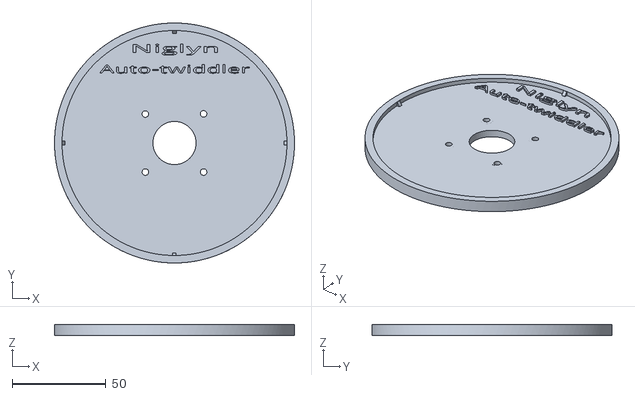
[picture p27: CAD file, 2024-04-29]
Patterson Tank Lid.stl
128.0 x 128.0 x 6.00

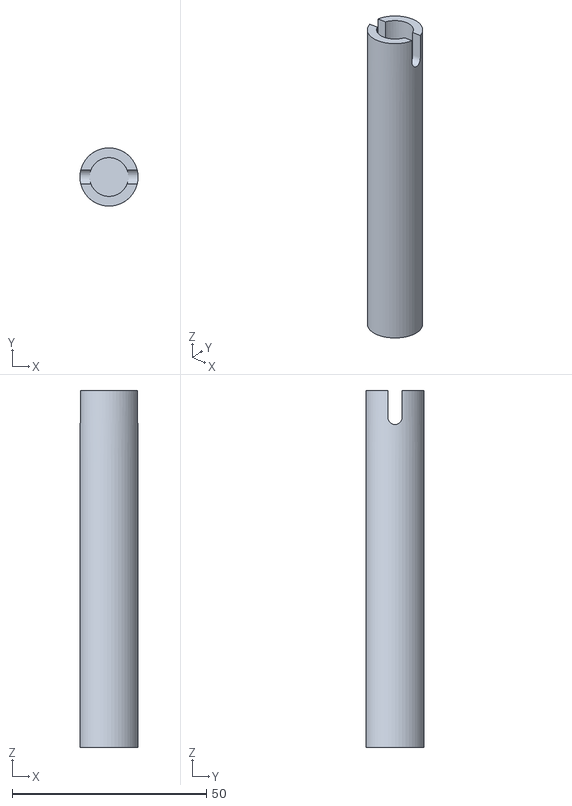
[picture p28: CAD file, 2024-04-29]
Twiddle stick v2.stl
15.0 x 15.0 x 92.0

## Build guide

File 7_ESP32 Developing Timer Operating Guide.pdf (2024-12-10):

I would really be grateful if you start to build the Developing Timer, that you go to the Photrio thread and say hi. Also please post photos of your completed tester.

Please refer to Photrio for further build help & to let us know you are building the timer.
Build a B&W film developing timer & twiddler - Cheap, Easy & it Works | Photrio.com Photography
Forums (https://www.photrio.com/forum/threads/build-a-b-w-film-developing-timer-twiddler-cheap-easy-it-works.204682/)

GitHub repository where all documentation & code can be found. billbill100 (github.com) (https://github.com/billbill100) V2.0 10/12/2024

### Developing Timer Operating Instructions

The Developing Timer works in exactly the same way as if one were using a standard timer or stopwatch.

However, by setting some basic parameters, the Developing Timer will step though each stage of the develop/stop/fix process, audibly and visually alerting the user that another operation is shortly due, or is taking place.

In this way, the user does not have to constantly watch the timer or have to remember when to stop developing or when and how long each agitation should be etc.

The Develop Timer is a modern take on the basic three-line LCD developing timers one can purchase, with dev/stop/fix times. Now using a modern colour display, easy time input with both visual & audible prompts & warnings.

It has been designed to be easy to use. Just press one knob to select the different times and turn the same knob to change them.

It is presumed the standard method of development timings are used. Developer is poured in and then the timer started. 10 seconds before end of development, the developer is poured out, with the Stop bath being poured in exactly at the end of development time.

First use after loading firmware.

Assuming the build has been completed correctly and the firmware loaded, when the Shutter Tester is connected to the computer via the USB cable (or another suitable power source), TFT & LCD should light & there will be output to the pc monitor.

Note in these steps, the terms ‘turn the encoder’ and ‘press the encoder’ are used.
For normal usage, the encoder is referred to as ‘the Blue Button’.

Enter User Key is to input the user-key. This is supplied free of charge upon request. Make a note of it, in case you ever perform a factory reset. Note the User Key has been added to prevent piracy and users being charged for downloads. The firmware is supplied free of charge and always will be.

Following the on-screen prompts, turn the encoder to show the User Key value. Then press the encoder.
If correct, the Shutter Tester will restart.

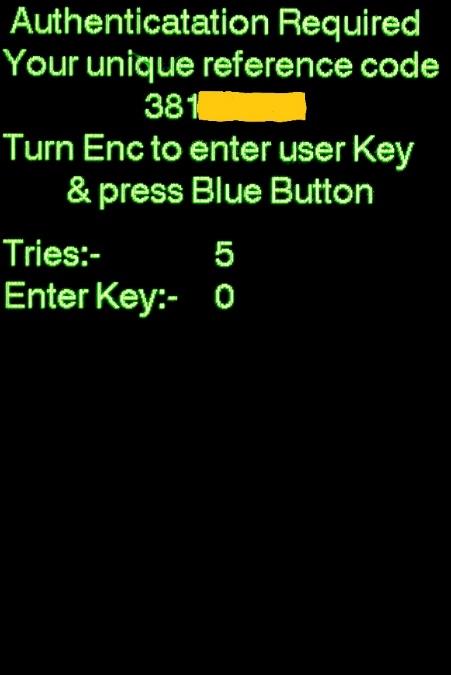
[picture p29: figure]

TFT showing user key input screen.

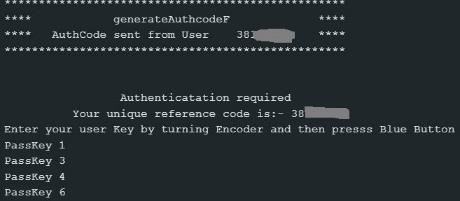
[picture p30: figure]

PC showing user key input screen.

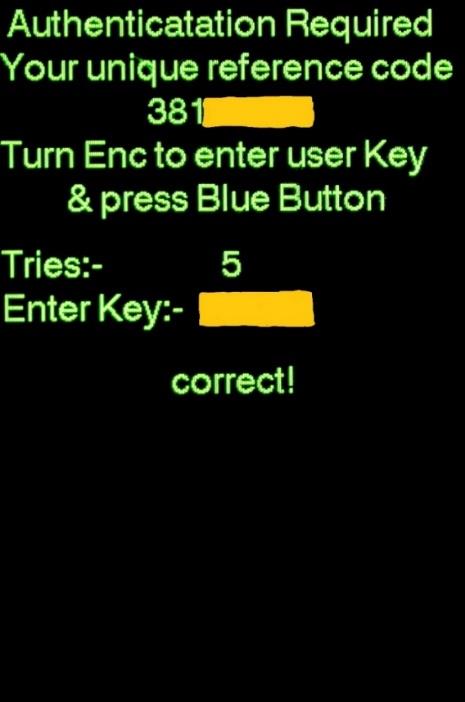
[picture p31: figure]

TFT showing user has input correct user key.

PC showing user has input correct user key.

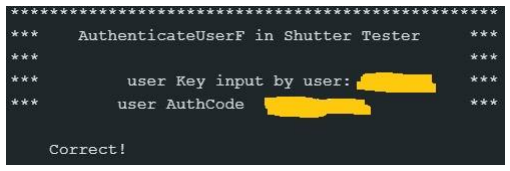
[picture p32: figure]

If the user key has been entered correctly, ‘Correct! Will be displayed’ and the Shutter Tester will restart in normal operation mode.

Note: - Sometimes a firmware upgrade will require the Shutter Tester is reset to default factory settings, so ensure you keep a note of your user-key.

Normal use.

To set the times:
Pressing the Blue knob once will place a red mark next to the Develop Time.
Turning the Blue knob will allow the developing time to be set. A maximum development time of 99 minutes 59 seconds can be set.

Pressing the Blue knob a second time, moves the red mark to the next line, Initial Agitate.
Turning the Blue knob will allow the Initial Agitation time to be set.

Pressing the Blue knob a third time, moves the red mark to the next line, Agitate Every.
Turning the Blue knob changes the interval between secondary agitations.

Pressing the Blue knob a fourth time, moves the red mark to the next line, Secondary Ag(itation) Time.
Turning the Blue knob changes the length of each secondary agitation.

Pressing the Blue knob a fifth time allows setting of the Stop bath time and a final press allows setting of the Fix bath time. A maximum time of 60 minutes can be set for these.

As an example, developing Ilford FP4 in ID11.
The developing time is set at 11 minutes.
Initial Agitation is 30 seconds
Secondary agitation is every 60 seconds (1 minute)
and each secondary agitation is performed for 10 seconds.

Note:- as with normal manual development, all timings are taken from development start. So initial agitation is from start of development time for 30 seconds. Secondary agitation interval (Agitate Every) is also taken from start of development time. So, in this example, agitations will take place exactly on the minute, for 10 seconds duration.

Stop bath has no programmable agitation times & it is usual for the stop bath to be continually agitated.
Visual prompt will be given, but there will be no audible warnings until 10 seconds before Fix Time ends. Auto-Twiddle, if selected, will turn for the whole Stop Bath time.

Fix bath gives initial agitation of 10 seconds and further agitations on the minute, of 10 seconds. Audible and visual notifications are given.
Auto-Twiddle, if selected, will turn for 10 seconds every minute

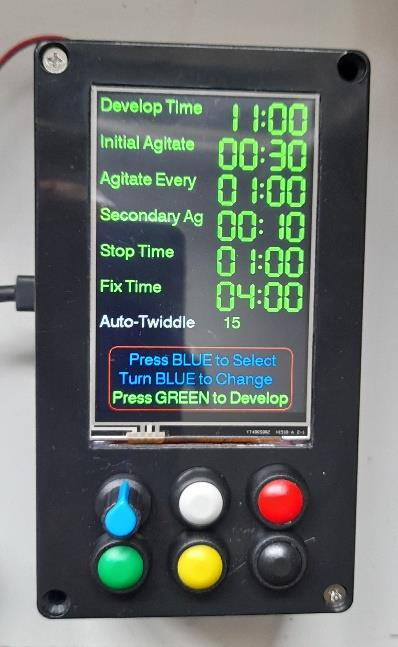
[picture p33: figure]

To start the Developing Sequence.

Pour in the developer & Press the Green button.

Immediately, Develop Time will start counting down.
At the same time, the Initial Agitation time will start to countdown, highlighted in Yellow/Red, with a deep pitch audible alert and on-screen prompt, requesting the user to start agitating.
This will continue until the Initial Agitation time has counted down to zero.
In our example, this will be from 11.00 minutes to 10.30 minutes, i.e 30 seconds.

The Agitate Every timer will also be counting down and 10 seconds before secondary agitation is due to take place, the Develop Time will change colour to Yellow and a high pitch audible alert will be heard, to notify the user that an an action, soon required.
In our example this will start at 10.10 and end at 10.00

When Agitate Every timer has counted down to 0, the Secondary Ag(itation time) will be highlighted Red/Yellow, with a deep pitch audible alert and on-screen prompt, requesting the user to start agitating.
(in our example, this will start at 10.00 and end at 9.50)

The sequence of Agitate Every and Secondary Ag(itation time) will repeat for the length of the developing time. In our example, 10 seconds before each complete minute, the high pitch warning will be heard & on the minute, a deep tone will be heard, prompting the user to start agitating.

Note: No agitations will be performed within the final 20 seconds of development time.

20 seconds before Develop Time ends, Develop Time will be highlighted in Yellow and a high pitch auditable tone heard, to warn the user that an action will be required in 10 seconds.

10 seconds before Develop Time ends, the tone will change to a deep tone, with an on-screen prompt, instructing the user to pour out the developer, A tri-tone will be heard at end of development time.

The Stop bath should be poured in immediately at the end of the development time. In our example, 11 minutes.

This completes the Developer cycle and the timer will pause, with an on-screen prompt, waiting for user input.

The Stop Bath.

When the Stop bath has been poured in, press the Green button.

The Stop Time will now count down for the allotted time.

As the stop bath is a very short duration & is normally agitated for the whole duration, the Stop Time will be highlighted Yellow/Red for the whole countdown period, but there will be no audible agitation warning.

10 seconds before the end, a deep pitch audible alert will be heard. At the end of Stop Time, a tri-tone will be heard & an on-screen message to pour out stop bath & pour in Fix bath.

The Fix Bath.

When the Fix bath has been poured in, press the Green button.

The Fix Time assumes standard fixing of agitation for the first 10 seconds and 10 seconds every minute.

For the first 10 seconds, Fix Time will be highlighted Yellow/Red, on-screen prompt & a deep audible tone, alerting the user to agitate.

For 10 seconds every minute, the same warnings will be given, whilst Fix Time counts down to 0.
At the end of which, a tri-tone will be heard & the screen will prompt to wash film.

Pressing the Black button will reset the Developing Timer, ready for another developing cycle.

Auto-Twiddler.

If the optional stepper motor is installed, it works as follows.

Pour in the developer and press the Green button to start development, tap the tank to dislodge bubbles and place the Auto-Twiddle mechanism onto the developing tank.

To start auto-twiddling Press the Yellow button. The Auto-Twiddle icon will turn yellow & run for the duration of Initial Agitate time.

When secondary agitations are required, the motor will automatically start to turn.

The speed of auto-twiddling is adjusted by turning the Blue knob during Development. The RPM is shown on the display.

The auto twiddler can be turned off at any time by pressing the Yellow button. Auto-Twiddle will turn Grey on the screen and the motor (if running) will stop. Pressing Yellow againthe button will re-activate auto-twiddling.

At the end of development, the auto-twiddler turns itself off and the Yellow button must be pressed for auto-twiddling if required during the Stop Bath process.

Similarly, at the end of the Stop Bath process, the auto-twiddler turns itself off and the Yellow button must be pressed for auto-twiddling if required during the Fix Bath process.

The design & build of the auto-twiddler mechanism is left up to the user. It is noted that the cheap Chinese developing tanks also raise and lower the film holding spiral during twiddling, which is an upgrade to the standard Paterson rotation only. Jobo & its clones have no provision for twiddling.

Important Notes.
It is important that the film is orientated correctly into the developing tank if twiddling (manual or auto). The film should be wound clockwise, starting from centre to the outside, when looking from above. This way, when twiddling (clockwise), fresh stock will be pulled into the film leading edge and pushed though the film.

Film wound & loaded clockwise in developing tank, when viewed from above

General Notes.
Initial agitation time cannot be set longer than development time – 20 seconds.

Secondary agitations will not be performed in the final 20 seconds of development.

Secondary agitation will not start until at least 20s after initial agitation has finished.

If the E-stop button is pushed whist motor is running, the motor will stop dead, with no deceleration.

To save the current settings, press and hold the Black button, press the Green button and release both. The Developing Timer give a high pitch tone. This can only be performed when not in a developing cycle.

To Factory Rest to default parameters, press and hold the Black button, press the Yellow button and release both. The Developing Timer will blow a raspberry & reset. This can only be performed when not in a developing cycle.

The Black button may be pressed & released at the end of the development or stop cycle & it will reset the Development Timer back to the setup screen.

The debate as to agitate by inversion or twiddling will go on forever.
With Patterson tanks, one has the choice of either twiddle or agitate.
Jobo have no provision for twiddling.
The Chinese tanks are designed be twiddled only and leak if inverted. A nice feature of these tanks is that they also slightly raise & lower the spool during twiddling.

From my own experimentation, I have found twiddling every bit as good as inversion, with the added benefit that there is no chance of chemical leaks or the lid popping off whilst inverted. It also stops over aeration of the Developer, especially if only developing one film in a multi-film tank (Patterson themselves warn of over vigorous agitation in this situation)

When using a water bath, as I always do, to maintain an even temperature, one does not get water everywhere during the agitations.

The water bath, I use for the rinse, as it is at the correct temperature, using the method Patterson describe. Auto-twiddling ensures that no errant chemical has found its way into the water bath.

I would really be grateful if you start to build the Developing Timer, that you go to the Photrio thread and say hi. Also please post photos of your completed tester.

Please refer to Photrio for further build help & to let us know you are building the timer.
Build a B&W film developing timer & twiddler - Cheap, Easy & it Works | Photrio.com Photography
Forums (https://www.photrio.com/forum/threads/build-a-b-w-film-developing-timer-twiddler-cheap-easy-it-works.204682/)

GitHub repository where all documentation & code can be found. billbill100 (github.com) (https://github.com/billbill100)

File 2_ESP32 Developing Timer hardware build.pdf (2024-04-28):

I would really be grateful if you start to build the Developing Timer, that you go to the Photrio thread and say hi. Also please post photos of your completed tester.

Please refer to Photrio for further build help & to let us know you are building the timer.
Build a B&W film developing timer & twiddler - Cheap, Easy & it Works | Photrio.com Photography
Forums (https://www.photrio.com/forum/threads/build-a-b-w-film-developing-timer-twiddler-cheap-easy-it-works.204682/)

GitHub repository where all documentation & code can be found. billbill100 (github.com) (https://github.com/billbill100)

## ESP32 Developer Timer Hardware Build V1.2 28/05/2024

Building the Developer Timer should be relatively easy. Below are some hints & advise on the build.

Refer to the ESP32 Wiring Guide schematic documents, for connections. Note. Schematics show a bare board, rather than it sitting in the breakout board.

All of the boards can be purchased from eBay, Amazon or AliExpress, which is by far the cheapest. Details of the parts required are detailed in the Parts List document

All of the boards are pre-soldered, you will not have to solder the components yourself. Most boards will also the header pins pre-soldered.

Using DuPont jumper wires, the boards can be connected together. You will need one packs of 10cm and one pack of 20cm Dupont wires to get the correct colour match.

Additionally, there are more Brown and Black wires used, so one pack of each, 20cm Brown & Black wires will be required.

There are many 3.3V (Brown)& GND (Black) power connections. These will not all fit into the breakout board screw-terminals. It will be necessary to connect them in groups with a choc-block or similar, then to the screw terminal. Alternately use the header pin specified in the parts document, although this will require soldering.

When fully built & tested, consider using a little hot-glue on the connectors, to stop them working loose.

ESP32 comes in either 30 or 38 pin boards. The parts list specifies the 38 pin nodeMCU32 and compatible 38 pin breakout board or the Lolin D32 board, which is 32 pin.

Ensure you pay particular attention to the polarity of the connections. The boards are clearly marked.
The breakout board legends are clearly marked for the nodeMCU32 processor board.

Caution if using the Lolin D32 board. This only has 32 pins. When fitting into the screw-terminal breakout board, ensure the front pins of the board align with the front pins of the breakout board. The rear three screw terminals on either side of the breakout board do not connect to anything. The legends on the breakout board do not correspond to the Lolin D32 pins,

The TFT is marked VDD (3.3V) and GND (0V). The tft board LED pin is also connected to 3.3V

The Encoder is marked 5V (connect this to 3V) and GND (0V)

Ensure the same Ground (0V) pins are used as shown in the schematic. Do not use the GND connection on the Node32, located between pin 19 and 21 or the bottom left GNS pin on the Lolin D32

To make the box
Ideally, the use of a milling machine with digital readout, makes it really easy to cut square holes in project boxes &

align all the drill holes. I have done this many times, but at present having only access to basic tools, another method was used. Please note the photos below are of the first prototype and was made using just the most basic of hand tools I was able to source. Whilst not the most professional looking, it does prove that much can be achieve with very little. Please be very careful when using the knife as detailed below.

The front of the box was covered in masking tape and the screen cut-out and button holes were drawn onto the tape. Note that the screen is smaller than the board it is mounted to, so only cut the hole to fit the screen. Do not make it too tight at the bottom. There are ribbon cables that must not be crushed.

There is only just enough room for the screen and two rows of buttons. The cut-out for the screen should be made such that the top of the tft pcb is touching the top of the inside of the box, so it is mounted as high as possible.

On the prototype, the bottom row of button holes were drilled slightly too high, so the buttons touch. There is space to slightly lower the button holes.

Using a Stanley knife and a metal straight edge, the pencil line was now repeatedly scored. Being very careful not to slip & cut one’s fingers or to cut past the pencil lines.

Ensure the box lid is clamped in a vice or similar and you use extreme care to always keep fingers BEHIND the blade, to avoid injury.

A new plasters trowel was used as the straight edge so one’s fingers can be kept well away from the blade.

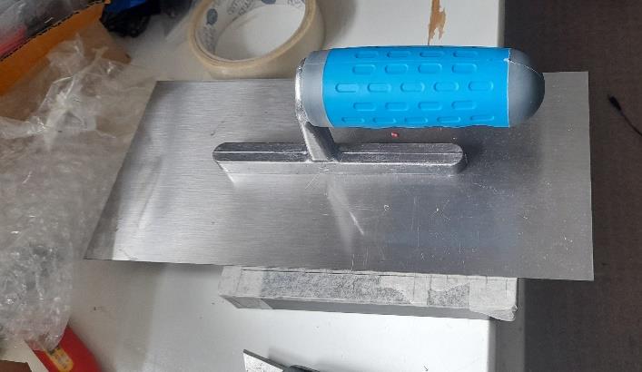
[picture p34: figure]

A series of overlapping holes were drilled inside the screen markings to remove the majority of the plastic.

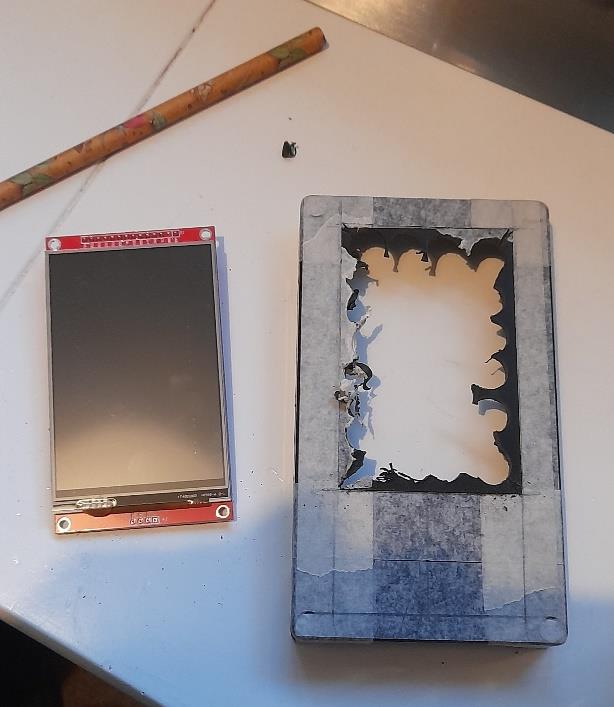
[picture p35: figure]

Using a junior hacksaw, or just a hacksaw blade, cut diagonally into the four corners, keeping the blade at 90 degrees

to the front of the box.

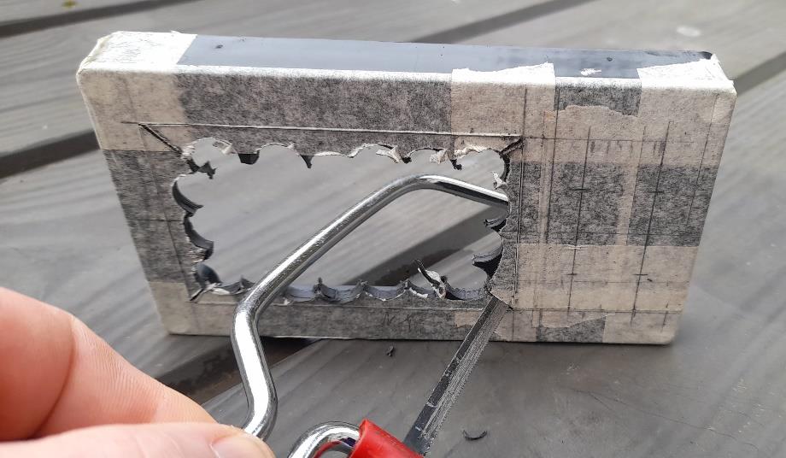
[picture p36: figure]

Turn the box over & using the saw marks as a reference, again score the inside of the box.

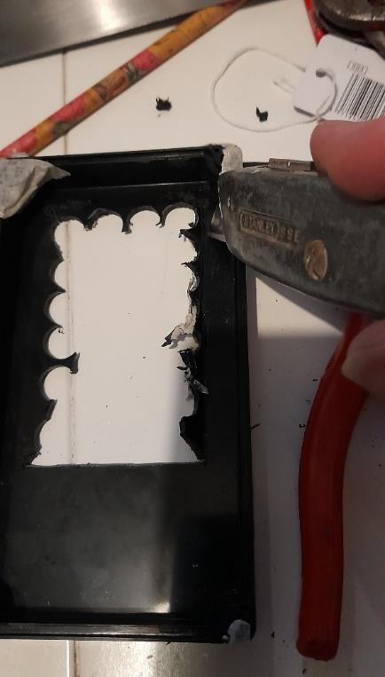
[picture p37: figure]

Using slip-joint pliers (as they fit into the opening) grip the lid at the score line and gently bend inwards. Do this all along the score line and repeat, each time bending a little more. Alternate this with scoring, which will get easier as the plastic bends. Eventually the plastic will snap away.

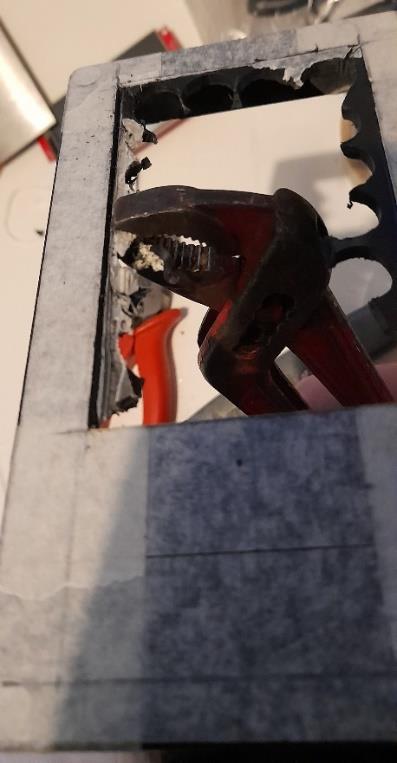
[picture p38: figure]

The stanley knife as shown below, can be used as a scraper by dragging the blade. It will smooth the rough edges and can be used to widen the hole if it is a bit tight for the screen to fit.
Make sure you are fully in control of the knife at all times to ensure it cannot slip & cause injury.

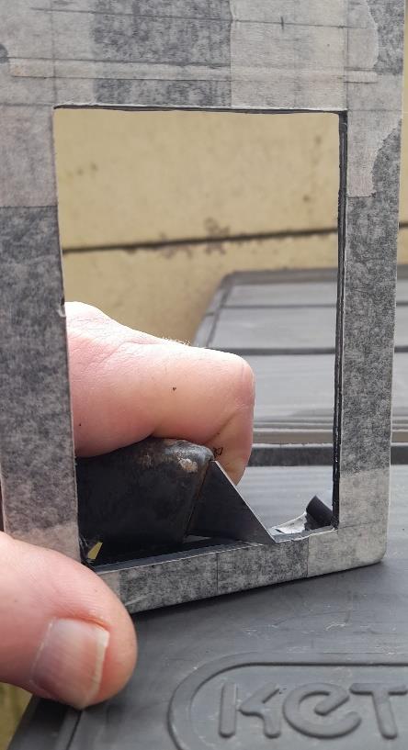
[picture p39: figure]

This of course, is only one method to make the cut-outs. One could use a jigsaw or fretsaw, for example.

The inside of the box was keyed using emery cloth to give a better adhesion for hot-glue. The screen was placed into position, face down, on a clean flat surface & hot glue used to secure it in place. Ensure hot-glue does not get onto the screen. The screen could also be mounted using bolts & the fixing holes in the pcb

Note the screen pcb is mounted as high as possible, to allow room for the buttons.

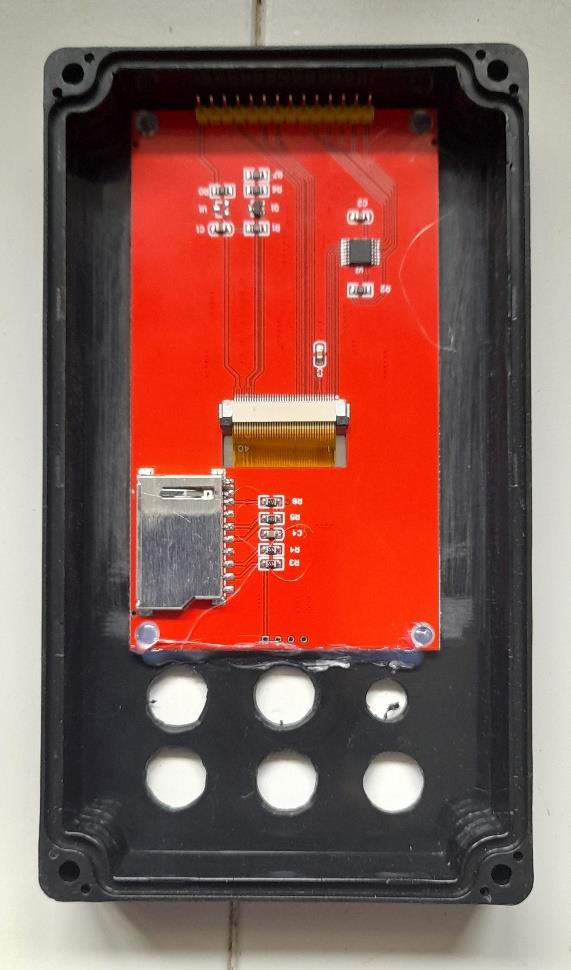
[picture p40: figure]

Drill the holes for the encoder (6mm) and the buttons (12mm) using a brad point drill bit.
Note the bottom line of button holes should be drilled a few mm lower than shown here, to give a little more separation.

Wooden blocks were cut to fit either side of the screen and slightly higher, to make a mounting platform for the breakout board. These were hot-glued in place and the breakout board glued to the wooden blocks. The breakout board could also be mounted using M3 bolts & mounting holes on the breakout board.

Note the following photos are of the Developing Timer, which uses a slightly different processor board & also a voltage regulator fitted in the base of the box.

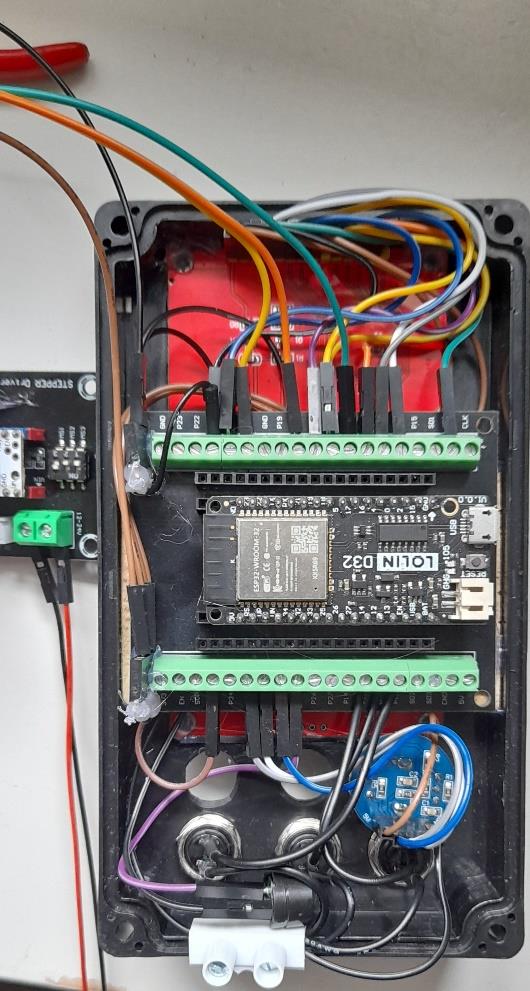
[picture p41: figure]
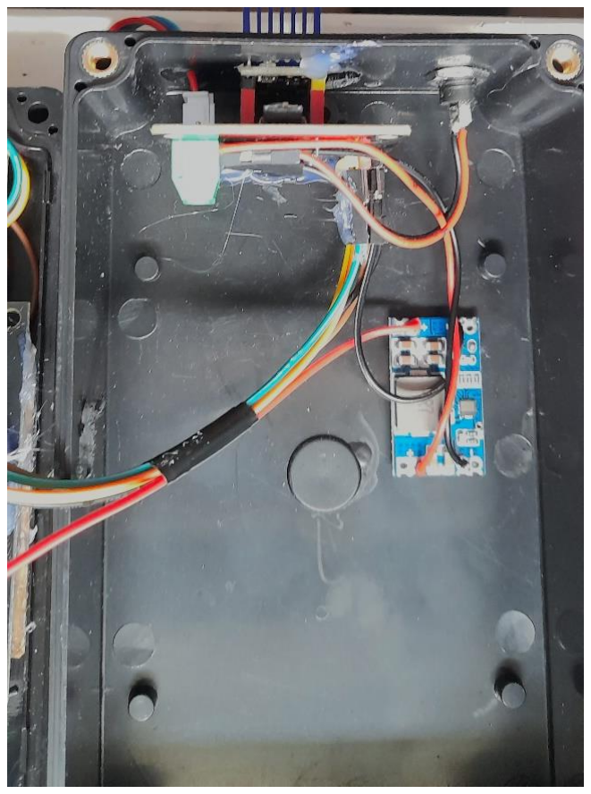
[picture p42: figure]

Stepper board hot-glued in position. M3 bolts will be used on the lower fixing holes for permanent mounting.
Note it really is a tight squeeze to fit the stepper motor into this size project box, but it can be done. An alternate is to use the next size project box (see link in parts list document).

Also shown is the 12V to 5V buck converter. As the stepper motor needs a 12C supply, using a buck converter to power the processor board, negates the need for a secondary USB power supply.

The finished box (minus two screws :o)

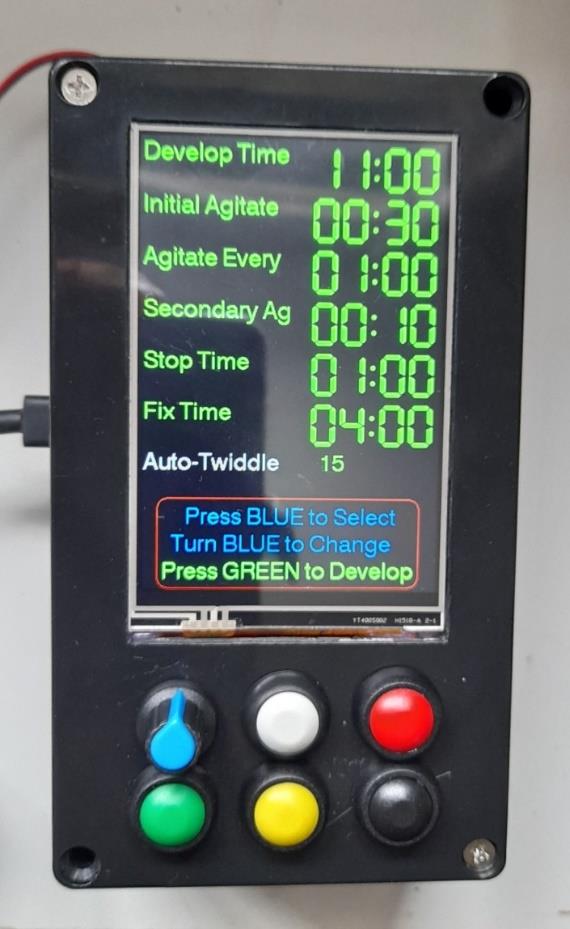
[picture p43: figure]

Template showing cut-out for screen & button positions.

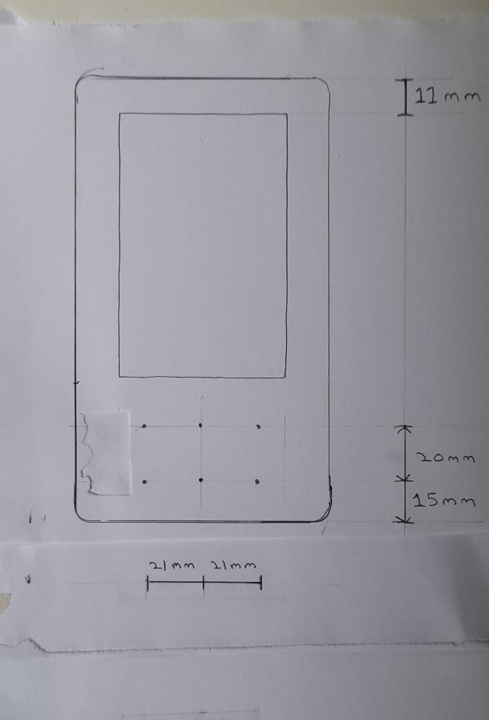
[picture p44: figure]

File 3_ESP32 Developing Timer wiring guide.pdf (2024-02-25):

I would really be grateful if you start to build the Developing Timer, that you go to the Photrio thread and say hi. Also please post photos of your completed tester.

Please refer to Photrio for further build help & to let us know you are building the timer.
Build a B&W film developing timer & twiddler - Cheap, Easy & it Works | Photrio.com Photography
Forums (https://www.photrio.com/forum/threads/build-a-b-w-film-developing-timer-twiddler-cheap-easy-it-works.204682/)

GitHub repository where all documentation & code can be found. billbill100 (github.com) (https://github.com/billbill100)

## ESP32 Developing Timer Wiring Guide V1.1 25/02/2024

Wiring of the modules is easily acclompished using Dupont wires. They come in a variety of lengths with terminals being male-male, female-female or male-female. Using a screw-terminal breakout board, male-female are most suitable, with a mix of 10 and 20cm lengths.

There are limited 3.3V and 0V (or GND) screw terminals available. One solution is to gather the 3.3V wires together, cut off the connector and remove a small piece of the insulation. Terminate all of the wires into a choc-bloc and then just one wire from the choc-bloc will go to the screw-terminal on the breakout board. The same is then done with the 0V wires.

Do not use the GND terminal between pins 19 & 21 on the NodeMcu32 board (it is an error on the board printing and is CMD, not GND) or the GND on the lower left of the Lolin D32 board.

Please refer to the schematic for details of all connections and use them in conjunction with the photographs below.

Please be aware that the photos below are of the 32 pin Lolin D32 board and it only uses 32 of the 38 screw connections (the rear 3 on either side are not used) and that the breakout board legends do not match that of the board.

The NodeMcu32 has more pins & uses all 38 screw terminals. Refer to the schematic for the correct connections. Note the outer two pins are not connected and there is also a non-conceted pin towards the cente of the tft screen.

Tft connections.

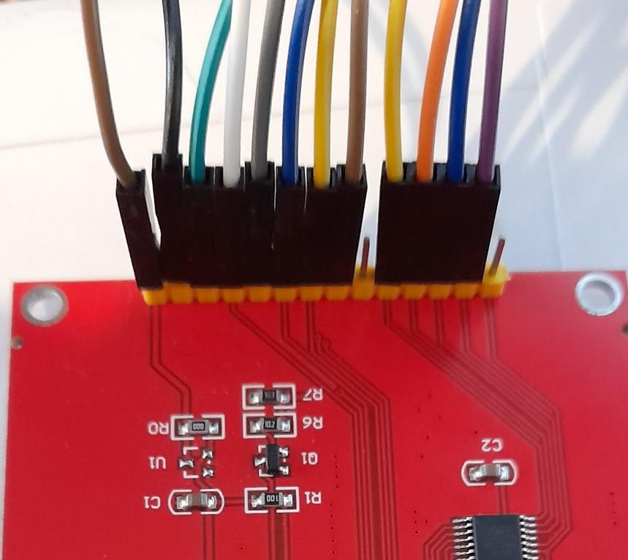
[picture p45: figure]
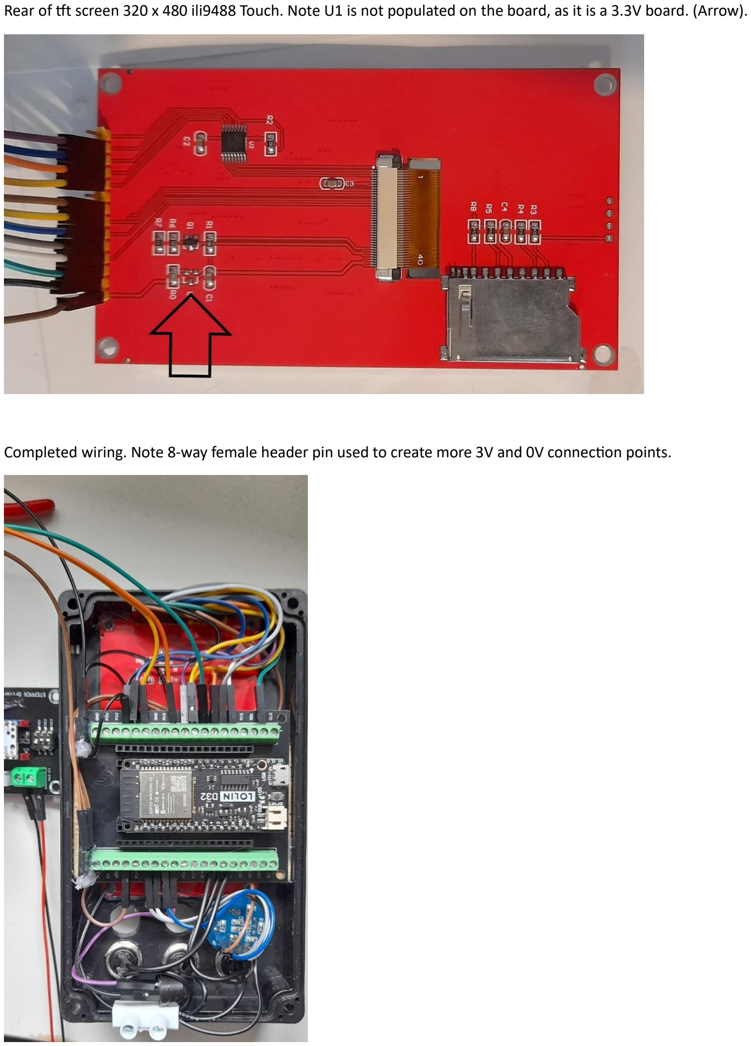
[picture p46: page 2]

Rear of tft screen 320 x 480 ili9488 Touch. Note U1 is not populated on the board, as it is a 3.3V board. (Arrow).

Completed wiring. Note 8-way female header pin used to create more 3V and 0V connection points.

Buttons & encoder wiring. Note the choc-bloc to combine the GND wires and the piezo sounder.

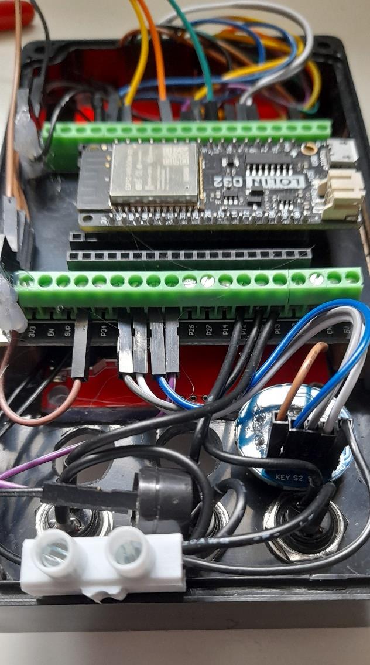
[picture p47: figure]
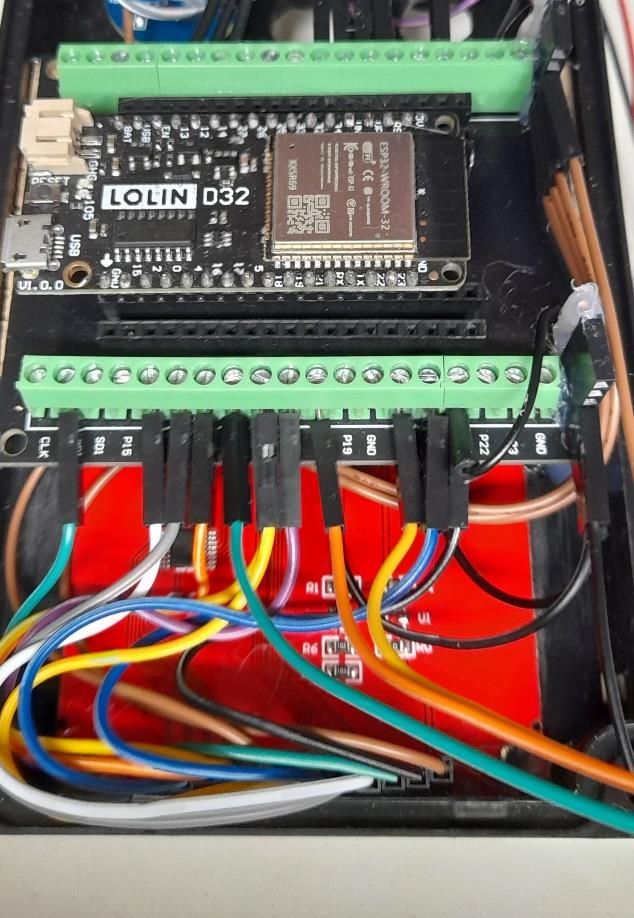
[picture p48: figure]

Tft screen & stepper wiring.

Stepper driver Board & plug-in stepper module.

The photo shows the older plug in module, which has the current adjusting potentiometer on the underside. The newer V2 has this mounted on the top & the board is black, rather than white, in colour.

The blue heatsink is attached by self adesive tape, which should already be afixed to the heatsink. The heatsink must be placed so that it is flush with the rear of the board (so the potentiometer & test holes are not obstructed) and placed centrually bettween the two rows of pins. Have a few trial runs before removing the adesive.

Note DIP switches, 1 is set to ON, 2 & 3 are set to OFF.
Version 1 driver board is shown (white) but version 2 should be used, as the adjustment potentiometer has been moved from the unserside to the top, for easier adjustment.

DO NOT CONNECT THE STEPPER DRIVER TO EITHER 12V POWER OR THE BREAKOUT BOARD WITHOUT SETTING THE CURRENT, AS DETAILED AT THE BOTTOM OF THIS DOCUMENT.

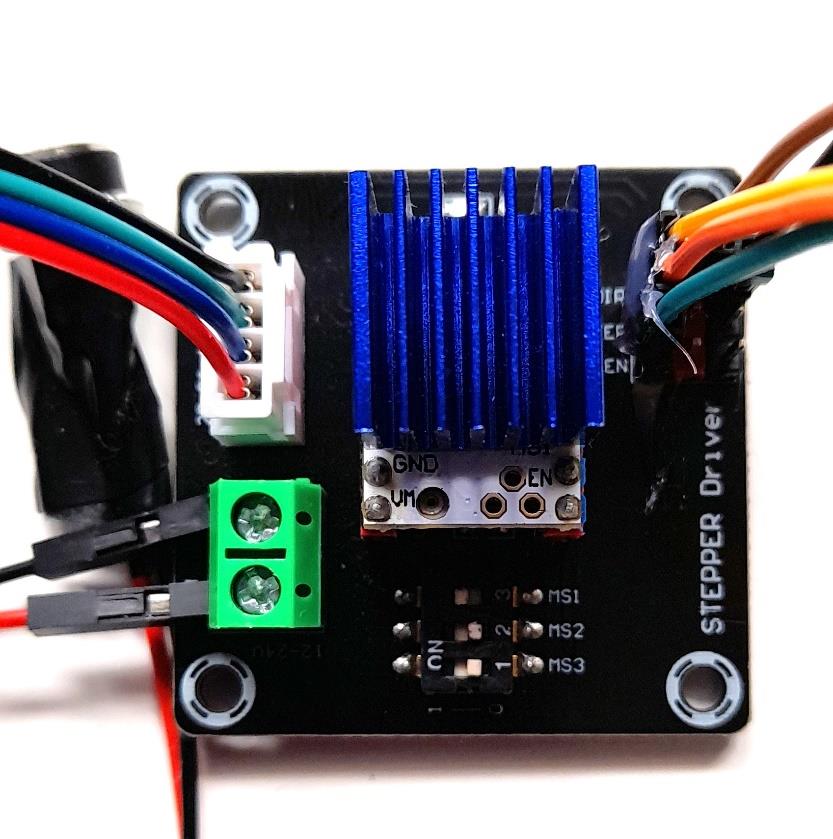
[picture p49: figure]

The heatsink is only held in place by adhesive tape, so care has to be taken that it is not knocked. The heatsink does not get too hot, so could be placed inside a suitable project box. For the prototype, it was mounted so the heatsink protrudes from the box, to facilitate this, both the power socket & header pins were desoldered from the board & re-soldered on the reverse.

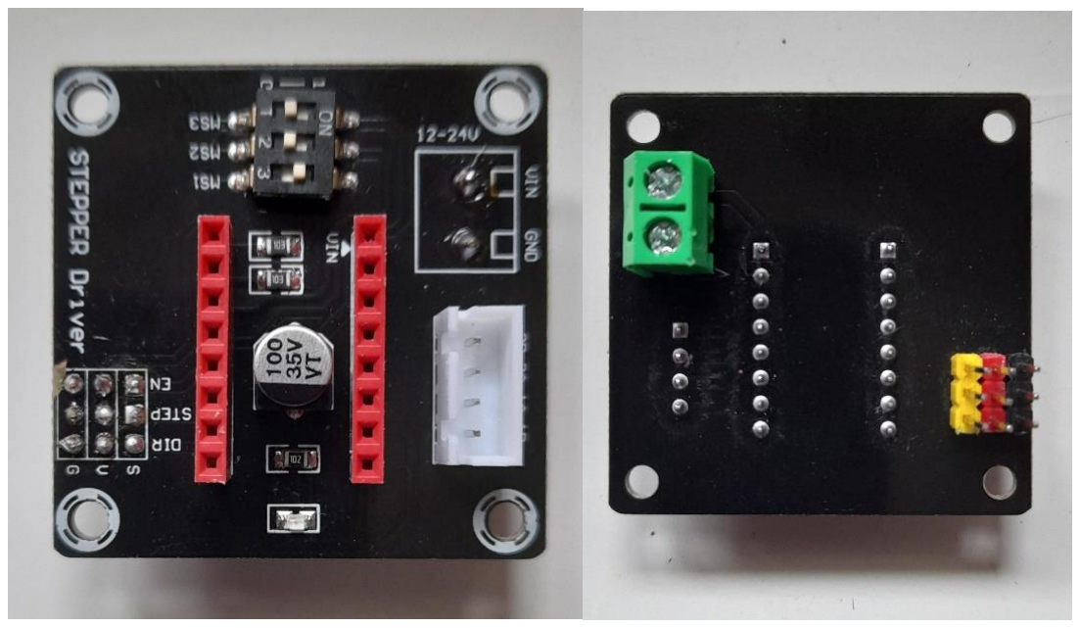
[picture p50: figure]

Green power socket & header pins mounted on reverse.

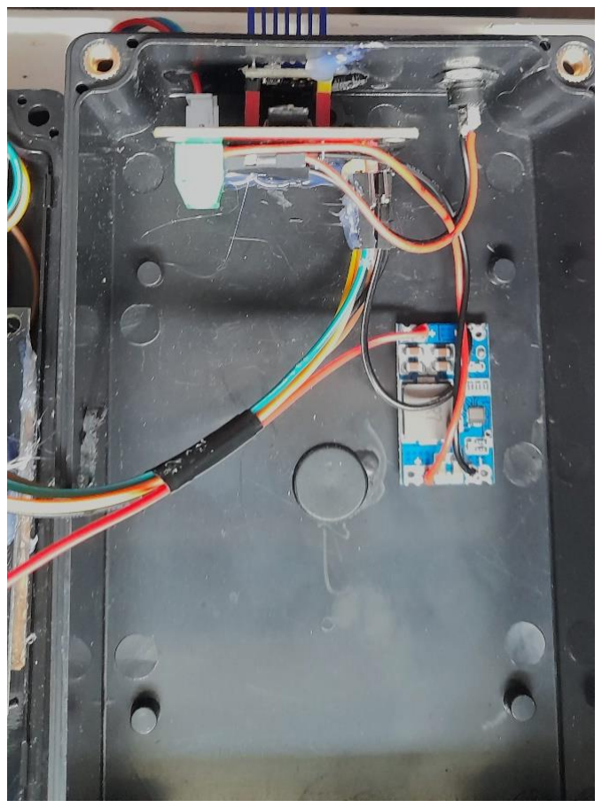
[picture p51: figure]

Stepper driver board mounted so heatsink is external. Note there is very little space in this project box to mount the driver board. It is recommended to use a larger project box if using the optional stepper driver board.

12V to 5V converter mounted in project box. This powers the processor board, negating the need for a separate USB power supply.

Completed project.

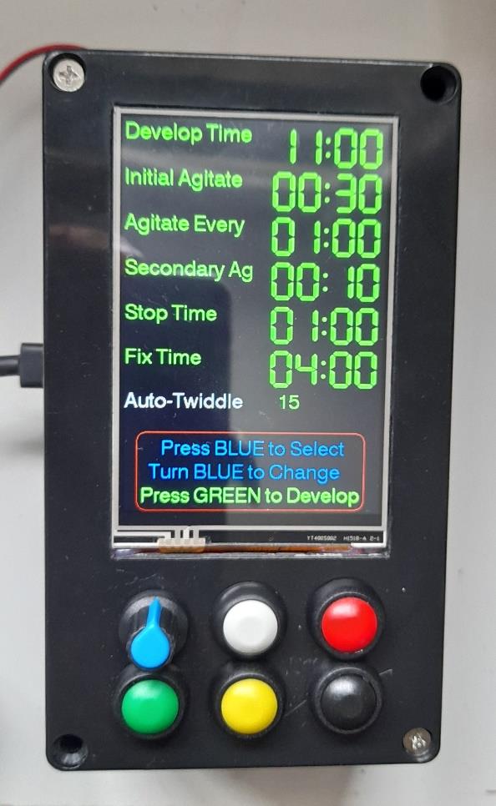
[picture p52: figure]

Important details for setting up stepper driver.

The current output of the stepper driver board must be set BEFORE connecting it to the stepper motor.

Ensure the stepper motor is disconnected and connect the 12V supply to the stepper board.

Using a multimeter set on the V DC range, connect it between GND and the gold-coloured circle, bottom right the stepper module.

Using a small screwdriver, turn the adjusting potentiometer until 0.8V is shown on the multimeter.

Disconnect all power before plugging in, or disconnecting the stepper motor cable. Failing to do so will destroy the stepper module.

Note the potentiometer works backwards, turning anti-clockwise increases the voltage, turning clockwise decreases it.

An alternate method if you do not have a multimeter, is to turn the potentiometer all the way clockwise.

Connect everything, including the stepper motor.

Set the Developing timer Initial Agitate to 11 minutes and start the timer.

Press the yellow button to activate the stepper motor.

Carefully turn the potentiometer anti-clockwise until the stepper motor runs smoothly.

Press the Yellow button to turn off the stepper motor. Press again to re-start. The motor should start smoothy, if not, turn the potentiometer a little more.

Monitor both the stepper motor body and stepper driver module for temperature. Whilst they will get warm, they should not get hot. If they are too hot, adjust the potentiometer clockwise, to reduce the current. Setting at 0.8 volts is a good starting point. If the motor struggles to twiddle, check nothing is binding & the motor is concentric with the twiddler. The voltage can be increased in small steps, if more power from the motor is required.

Here is a good video describing how to set the TM32208 stepper driver module.

8.08 to 11.150

TMC2208 3 Ways - Part 1 (youtube.com) (https://www.youtube.com/watch?v=TubpTMFkbVs)

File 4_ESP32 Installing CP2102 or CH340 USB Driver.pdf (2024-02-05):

## Installing CP2102 or CH340 USB Driver. V1.2 21/01/2024

Note:- These guides must be followed in the correct order
ESP32 Installing CP2102 USB Driver
ESP32 Arduino Software Load (not required for Development Timer)
ESP32 Firmware Load

The CP2102 device driver does not normally come pre-installed on Windows and has to be installed manually. Note:- If using a ESP32 board with a different driver, Windows may or may not have a driver pre-loaded.

The CH340 driver will normally install on a Windows computer. This driver is required if using the Lolin D32 board for the Development timer. Follow the below to see if Windows has the CH340 driver. If not, skip t the end of this document for CH340 specific instructions

Connect the ESP32 board to the computer using a suitable USB cable.

Open Device Manager by pressing Windows Key + X and selecting ‘Device Manager’

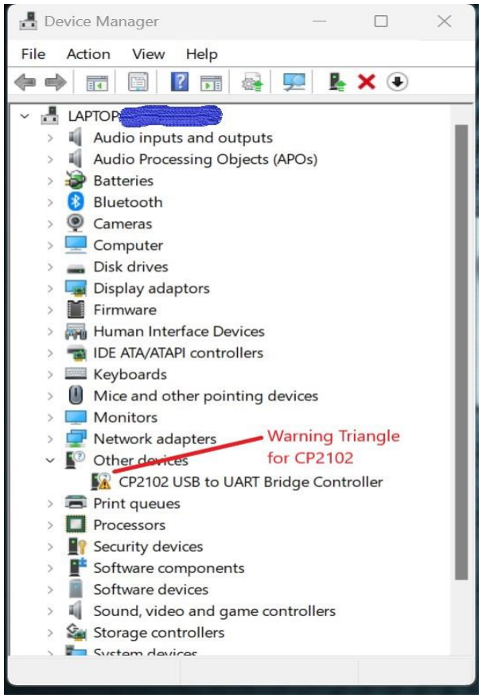
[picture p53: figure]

If you see a yellow ! triangle labelled CP2102, then drivers require installing.

Note:- the Ports (COM & LPT) may need expanding, to see the device.

Note:- if using a board with the CH340 USB device (Lolin D32) & the above is not showing it as working, skip to the end of this document for CH340 specific guidance.

Step 1,

Download the drivers from the link below.

Fow Windows users, select the top one, CP210x Universal Windows Driver

CP210x USB to UART Bridge VCP Drivers - Silicon Labs (silabs.com) (https://www.silabs.com/developers/usb-to-uart-bridge-vcp-drivers?tab=downloads)

Step 2,

Navigate to the downloaded file (most likely in Downloads directory) Highlight it by clicking once, then right-click and select ‘Extract All’ and accept the default directory.

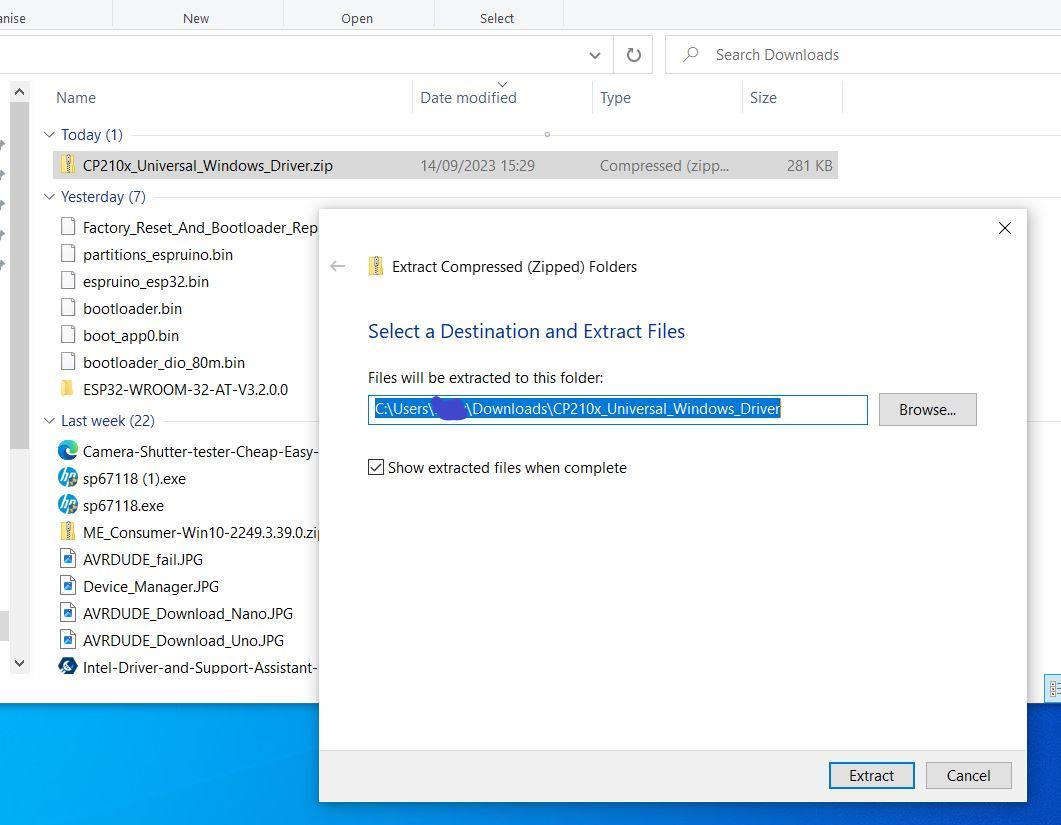
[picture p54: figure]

Step 3,

Go back to Device Manager and right-click on the Yellow ! Triangle select ‘Update Driver’ and then ‘Browse my computer for drivers’

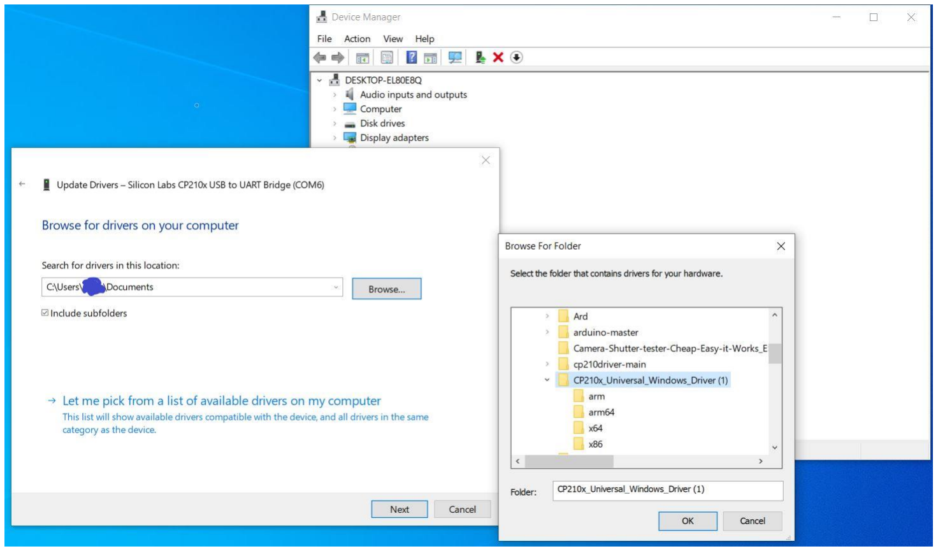
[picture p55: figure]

Click ‘Browse’ and navigate to the Downloads folder, find and click on the folder that was previously downloaded & extracted.

Click ‘Ok’ and then ‘Next; in the previous box and the drivers should be installed.

A computer re-start will be required to complete installation.

CH340 Specific Instructions.

If the CH340 driver is not loaded & Windows is not showing an option to automatically install it, follow the link below for a video guide.

How to Install CH340 Drivers - SparkFun Learn (https://learn.sparkfun.com/tutorials/how-to-install-ch340-drivers/all)

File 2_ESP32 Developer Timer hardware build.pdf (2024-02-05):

## ESP32 Developer Timer Hardware Build V1.0 B 05/02/2024

Building the Developer Timer should be relatively easy. Below are some hints & advise on the build.

Refer to the ESP32 Wiring Guide schematic documents, for connections. Note. Schematics show a bare board, rather than it sitting in the breakout board.

All of the boards can be purchased from eBay, Amazon or AliExpress, which is by far the cheapest. Details of the parts required are detailed in the Parts List document

All of the boards are pre-soldered, you will not have to solder the components yourself. Most boards will also the header pins pre-soldered.

There is a choice of two processor boards to use. These are detailed in the parts document. The Lolin board has the advantage of battery backup, but does require the heard pins to be soldered.

Using DuPont jumper wires, the boards can be connected together. You will need two packs of 20cm Dupont wires to get the correct colour match. Optionally also using a pack of 10cm wires for the shorter wire runs, will make a neater build.

Additionally, there are more Brown and Black wires used, so one pack of each, 20cm Brown & Black wires will be required.

There are many 3.3V (Brown)& GND (Black) power connections. These will not all fit into the breakout board screwterminals. It will be necessary to connect them in groups with a choc-block or similar, then to the screw terminal. Alternately use the header pin specified in the parts document, although this will require soldering.

When fully built & tested, consider using a little hot-glue on the connectors, to stop them working loose.

ESP32 comes in either 30 or 38 pin boards. The parts list specifies the 38 pin nodeMCU32 and compatible 38 pin breakout board or the Lolin D32 board, which is 32 pin.

Ensure you pay particular attention to the polarity of the connections. The boards are clearly marked.
The breakout board is also marked for the nodeMCU32, but these do not match the Lolin board, so be very careful that the correct connections are made.

The TFT is marked VDD (3.3V) and GND (0V). The tft board LED pin is also connected to 3.3V

The Encoder is marked 5V (connect this to 3V) and GND (0V)

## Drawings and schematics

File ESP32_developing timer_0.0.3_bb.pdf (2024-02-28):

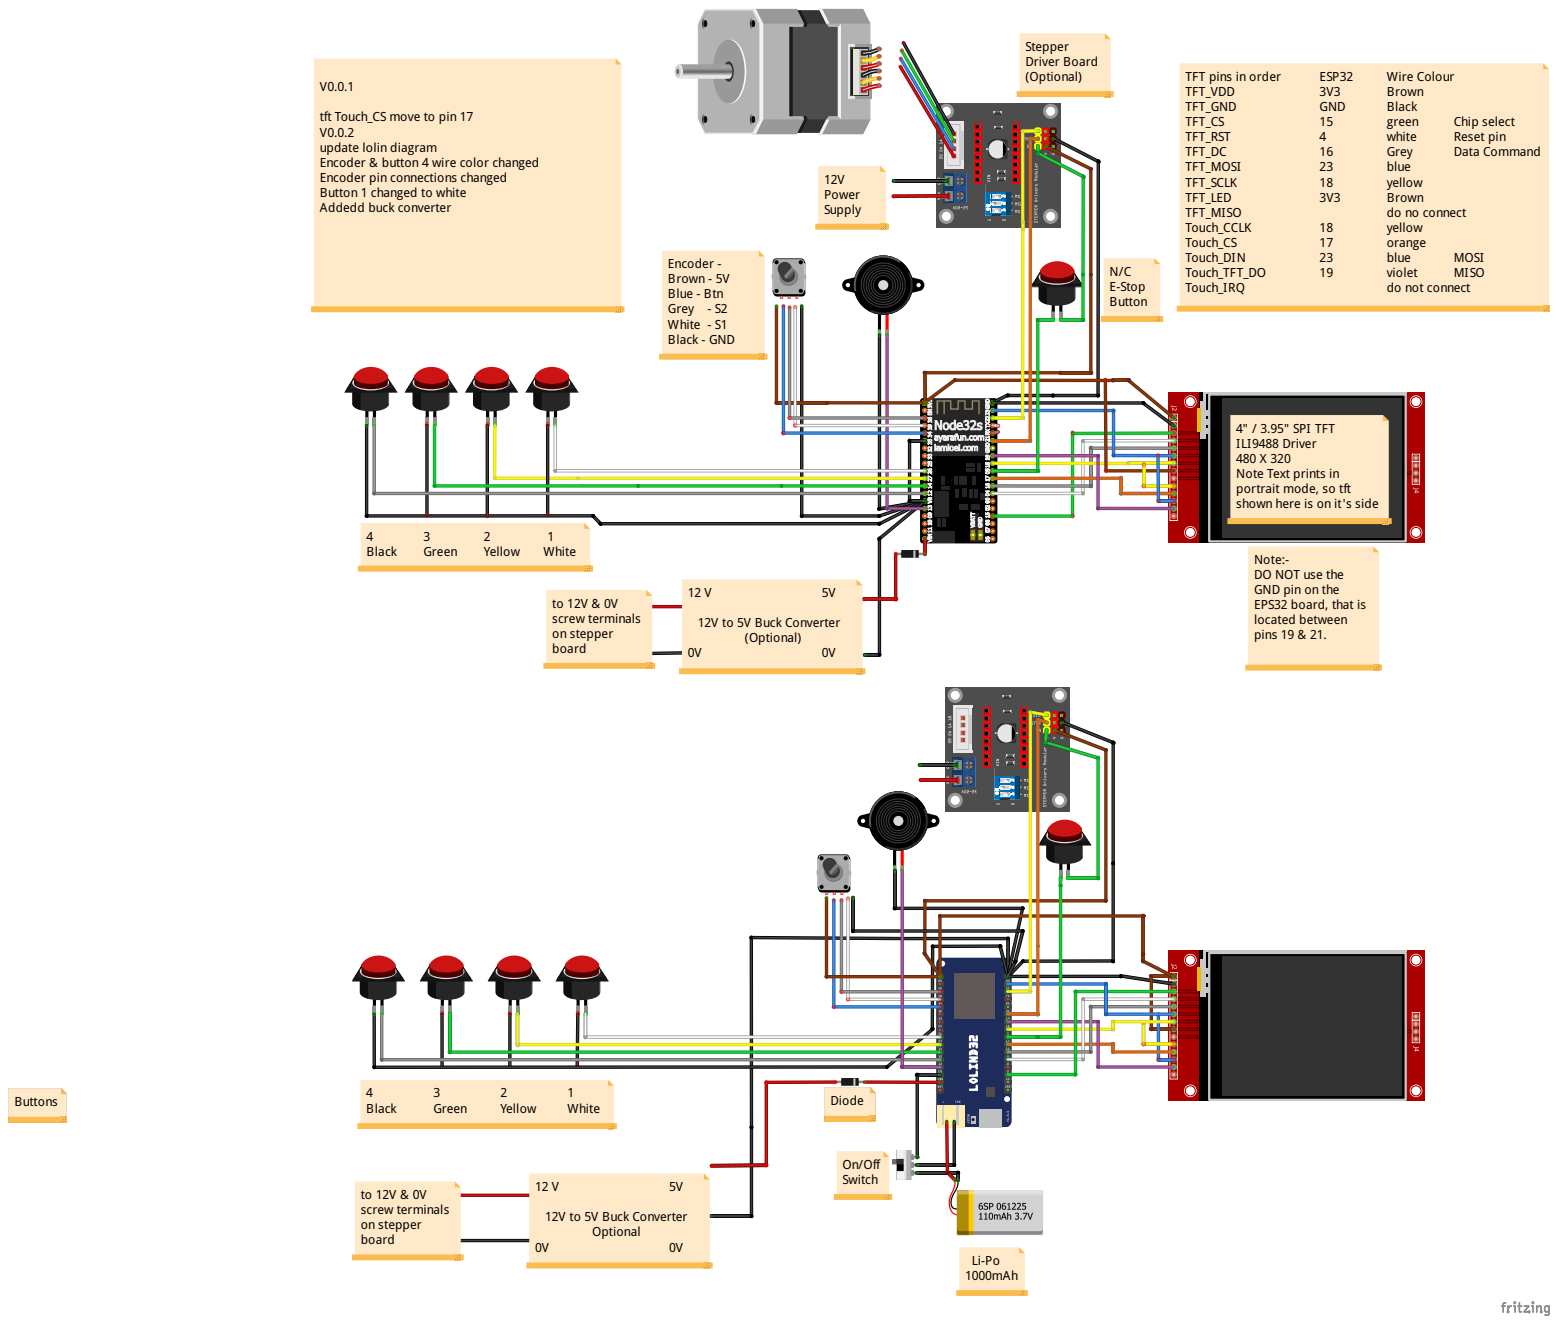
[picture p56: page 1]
Black; Green; Yellow; White; TFT pins in order; ESP32; Wire Colour; TFT_VDD; Brown; TFT_GND; GND; TFT_CS; green; Chip select; TFT_RST; white; Reset pin; TFT_DC; Grey; Data Command; TFT_MOSI; blue; TFT_SCLK; yellow; TFT_LED; TFT_MISO; do no connect; Touch_CCLK; Touch_CS; orange; Touch_DIN; MOSI; Touch_TFT_DO; violet; MISO; Touch_IRQ; do not connect; Li-Po 1000mAh; 12V Power Supply; Stepper Driver Board (Optional); N/C E-Stop Button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

tft Touch_CS move to pin 17
update lolin diagram
Encoder & button 4 wire color changed
Encoder pin connections changed
Button 1 changed to white
Addedd buck converter

4" / 3.95" SPI TFT
ILI9488 Driver
Note Text prints in
portrait mode, so tft
shown here is on it's side

Note:-
DO NOT use the
GND pin on the
EPS32 board, that is
located between
pins 19 & 21.

12V to 5V Buck Converter
